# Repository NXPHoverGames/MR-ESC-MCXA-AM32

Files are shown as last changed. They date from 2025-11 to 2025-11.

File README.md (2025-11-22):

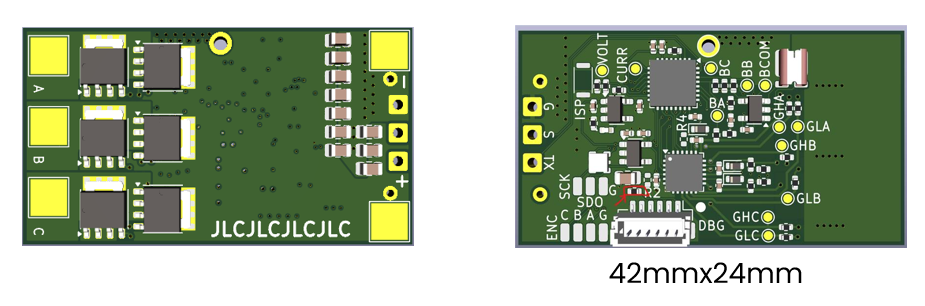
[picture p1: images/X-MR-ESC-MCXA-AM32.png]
Rendering of x-MR-ESC-MCXA-AM32 board


MR-ESC-MCXA-AM32 is a proof of concept Drone motor ESC (Electronic Speed Controller) motor controller, 
using NXP MCXA153 MCU and running the opensource AM32 software.

NOTE: This design is not supported by NXP motor control framework tools 
(it could of course be made to run with modifications)

Design files are in KiCAD.

Target MCU in AM32 directories is "a153"
Upstream repository for AM32 is here:
https://github.com/AlkaMotors/AM32-MultiRotor-ESC-firmware/tree/master

Interim AM32 enablement for MR-ESC-MCXA-AM32 is here:
(It will be upstreamed)
repo:NXPHoverGames/AM32-MultiRotor-ESC-firmware-MCXA
https://github.com/NXPHoverGames/AM32-MultiRotor-ESC-firmware-MCXA

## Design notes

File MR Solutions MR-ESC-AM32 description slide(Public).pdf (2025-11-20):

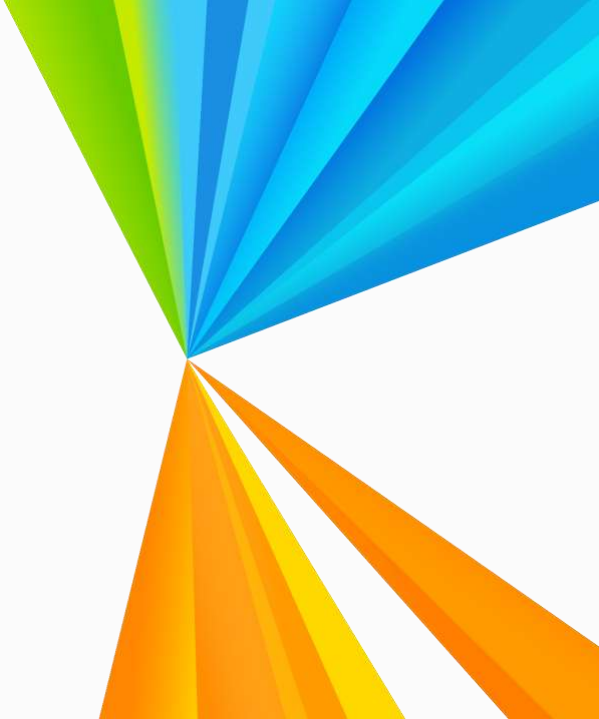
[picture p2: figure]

| Public | NXP and the NXP logo are trademarks of NXP B.V. All other product
or service names are the property of their respective owners. © 2024 NXP B.V.

## Iain Galloway Mobile Robotics, System Innovations CTO R&D

## March 2025

## Proof of concept MCX ESC using AM32

opensource software.

# NXP Mobile Robotics

# MR-ESC-AM32 Proof of Concept only

## MCXA MCU: NXP MCXA153

- Simple trapezoidal ESC motor controller with RC-PWM input.
- Form factor for Drones and small devices.
- Copy of AM32 reference hardware to establish NXP Baseline
- Low cost ~$10 target
Justification:
- AM32 is popular opensource ESC software.
- Engage with community
- Include NXP Solution in NXP HoverGames drone EVK
- Future MR-HGK-RT
- Hooks in place for QDEC where odometry is needed such as ground applications. MR-B3RB-M, MELM.
Specs –approx.:
- 5.5V up to 24V, 6 Cell/6S LiPo battery input voltage
- Onboard PSMN1R4-40 FETs rated 240A
– note this is not the board rating
- 50A peak drain seems likely
- In-situ current rating TBD, required validation testing, dependent on heatsinking added.
Future potential options:
- Enable QDEC input
- Enable NXP software
- Revise design to use MCXA16x
(Analog integration lower bom cost)
- Enable NXP FOC as alternative software.
- Add CAN interface
- Consider advanced version using MCXN with FOC, NPU enable motor analysis, T1 Ethernet interface

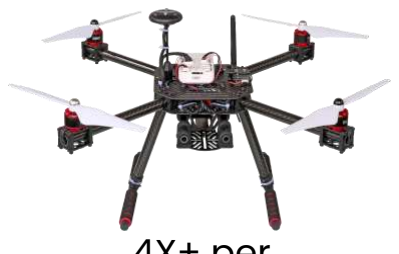
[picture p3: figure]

## 4X+ per Drone

MCU | Gate Driver
RC-PWM | FETs

Simple
Trapezoidal

Approx BOM
$1.68 MCU
$0.75 Gate Drv
$0.13 opAmp
$6.40 FETs 8x$0.80*
$0.18 regulator
$0.18 regulator
$1-2 PCB, passives, connectors -=-=-
$11.42
*FET selection is cost driver.

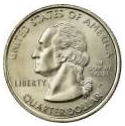
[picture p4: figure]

42mmx24mm

3 | NXP | Internal

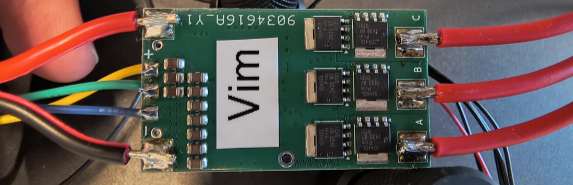
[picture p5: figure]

Wire the + and - input to the power supply (6V to 24V max). The board does not have polarity protection so make sure you have wired the + and - correctly.

Wire signal pin (indicated with "S" on board) to the function generator which should generate a PWM signal with Low voltage at 0V and High voltage at 3.3V. PWM signal must have a period of 2.2ms. Motor starts spinning from 50% duty cycle up to 99%.

Wire ground pin (indicated with "G" on board) to the ground of the function generator.

TX pin may connect to a serial data converter (e.g. FTDI cable). This is not mandatory for the board to work.

Wire motor phase outputs (A, B and C) to each motor phase.

Test pads:

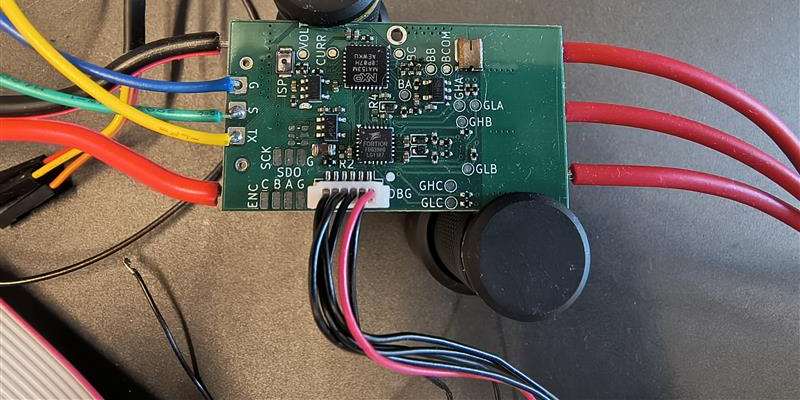
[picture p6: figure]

- Test pad GHA, GHB and GHC are the high MOSFET gate signals of each corresponding phase.
- Test pad GLA, GLB and GLC are the low MOSFET gate signals of each corresponding phase.
- Test pad BA, BB and BC are the BEMF signals of each corresponding phase.
- Test pad BCOM is the BEMF common signal.
- Test pad VOLT is tied to the voltage sense input of the MCU.
- Test pad CURR is tied to the current sense input of the MCU.

# Wiring (DRAFT – for debugging purposes)

For debug purposes you can optionally use the pads "ENC A" and "ENC C" as GPIO. The "G" pad near the ENC pads is a ground.

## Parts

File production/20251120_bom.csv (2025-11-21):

Designator | Footprint | Quantity | Value | LCSC Part #
C1, C10, C15, C2, C3, C4, C5, C6, C7, C8, C9 | 0805 | 11 | 10uF 35V
C12, C19, C23 | 0402 | 3 | 1uF 16V
C13, C14, C16, C24, C25 | 0402 | 5 | 100nF 16V
C17, C20, C21 | 0603 | 3 | 1uF 50V
C18, C22 | 0402 | 2 | 100nF 50V
D1, D2, D3 | D_SOD-523 | 3 | 1N4148WT
D4 | 0402 | 1 | LED GREEN
J13 | JST_SH_BM06B-SRSS-TB_1x06-1MP_P1.00mm_Vertical | 1 | DEBUG
Q1, Q2, Q3, Q4, Q5, Q6 | LFPAK56 | 6 | PSMN1R4-40YLDX
R1, R10, R11, R12, R13, R24, R3, R8, R9 | 0402 | 9 | 10k
R14, R15, R16, R22 | 0402 | 4 | 1k
R17, R18, R19, R5, R6, R7 | 0402 | 6 | 20
R20 | 0402 | 1 | 100k
R21 | WSK1216 | 1 | 1m 3W
R23 | 0402 | 1 | 2.2k
R25 | 0402 | 1 | 100R
SW1 | TS2306A | 1 | ISPMODE
U1 | SOT-23-5 | 1 | TPS7B92033DBVR
U2 | VQFN-24-1EP_4x4mm_P0.5mm_EP2.45x2.45mm | 1 | DRV8300N or FD6288 or equivalent
U3 | HVQFN-32-1EP_5x5mm_P0.5mm_EP3.1x3.1mm | 1 | MCXA1xxVFM
U4 | SOT-23-5 | 1 | TPS7B92050DBVR
U5 | BB-2020BGR-TRB | 1 | BB-2020BGR-TRB
U6 | SOT-23-5 | 1 | INA180B1

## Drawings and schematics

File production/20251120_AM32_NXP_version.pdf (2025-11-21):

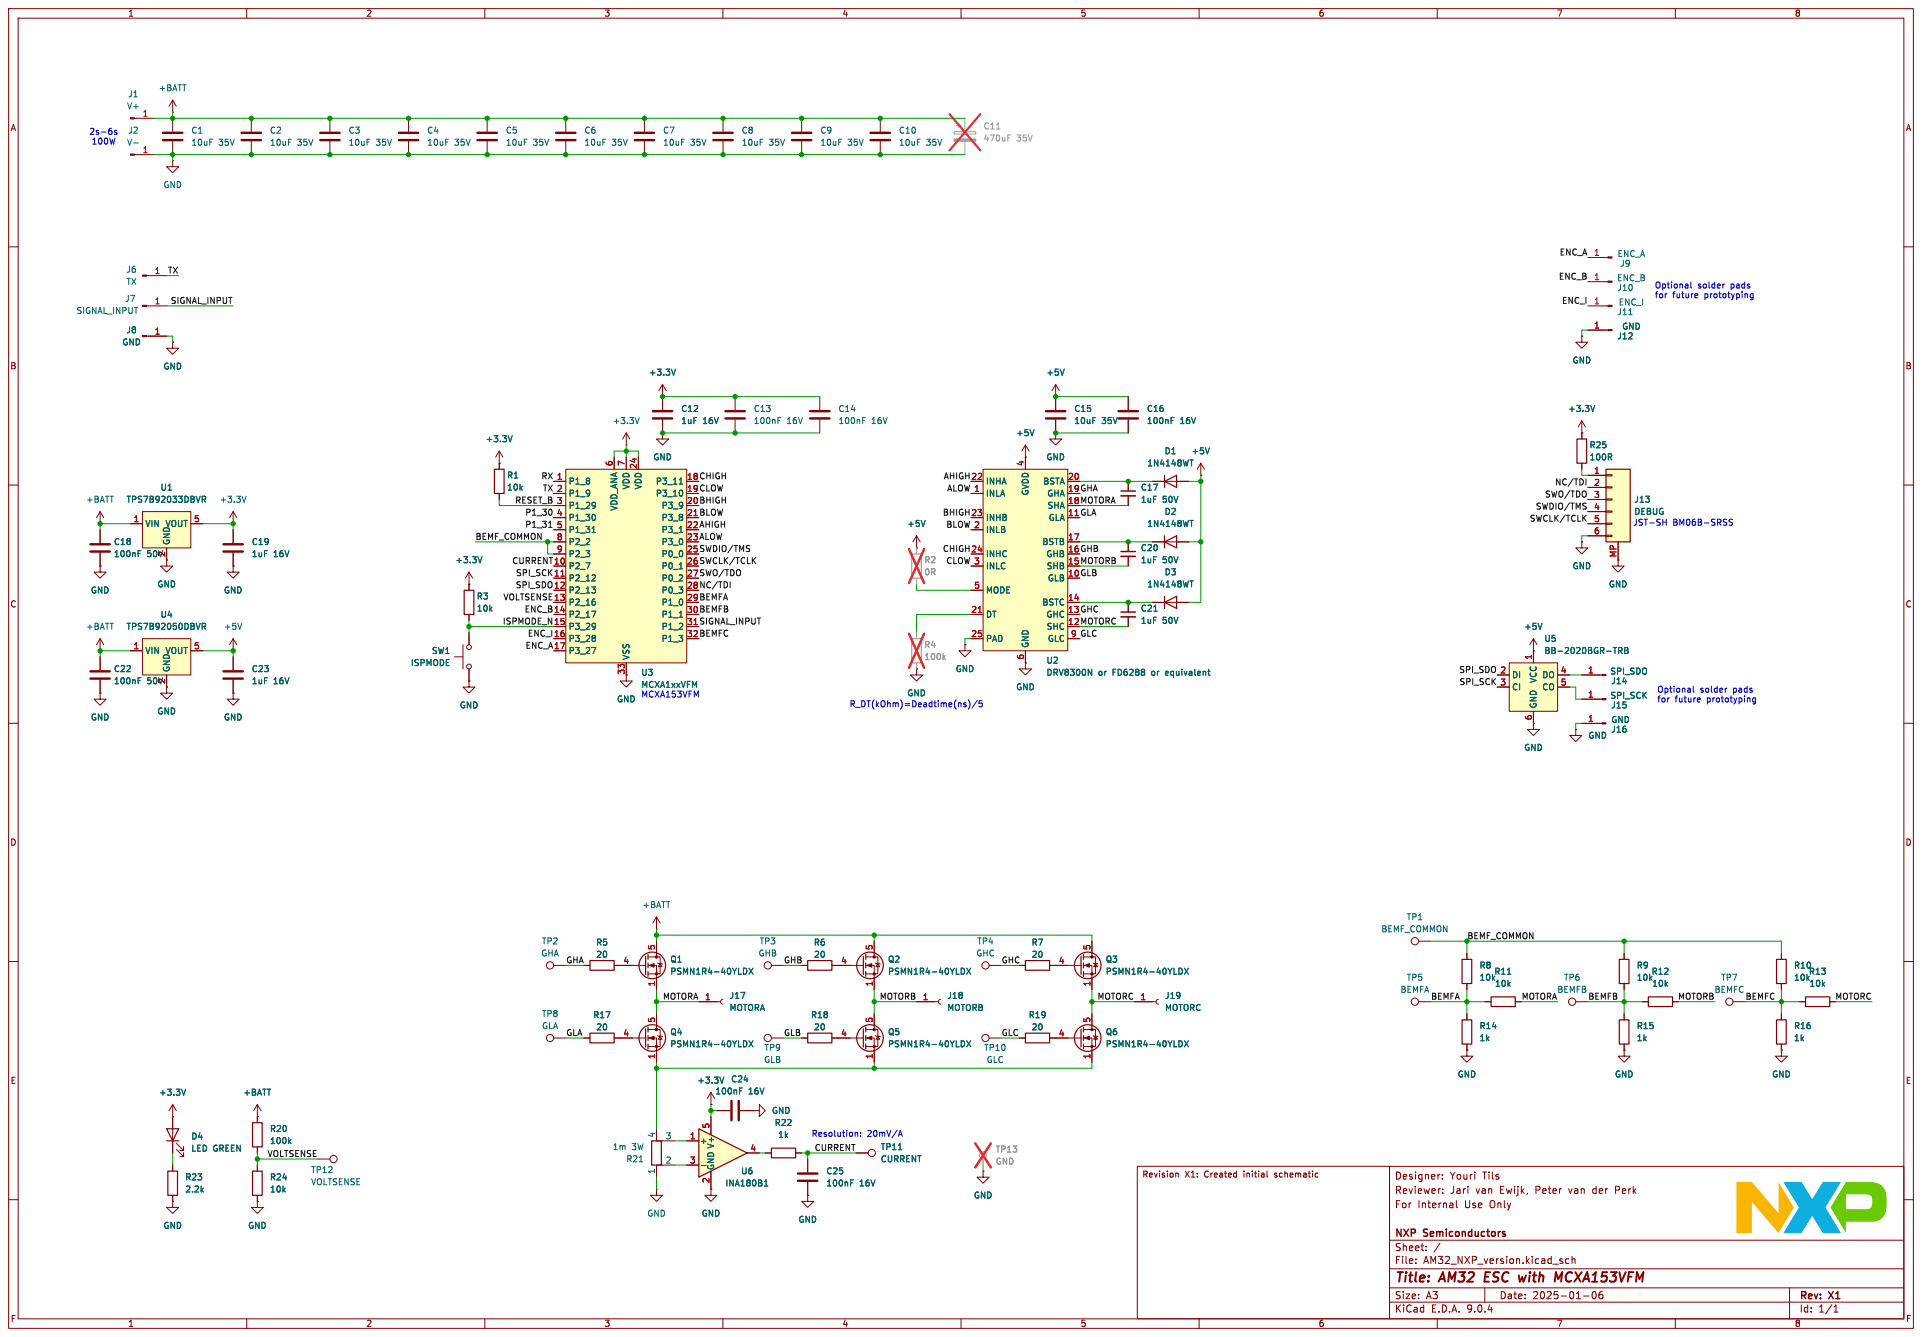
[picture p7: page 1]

6 BSTA 20 GHA 19 SHA 18 GLA 11 BSTB 17 GHB 16 SHB 15 GLB 10 BSTC 14 GHC 13 SHC 12 GLC 9 U2 DRV8300N or FD6288 or equivalent D3

6 BSTA 20 GHA 19 SHA 18 GLA 11 BSTB 17 GHB 16 SHB 15 GLB 10 BSTC 14 GHC 13 SHC 12 GLC 9 D3

Id: 1/1 Title: AM32 ESC with MCXA153VFM

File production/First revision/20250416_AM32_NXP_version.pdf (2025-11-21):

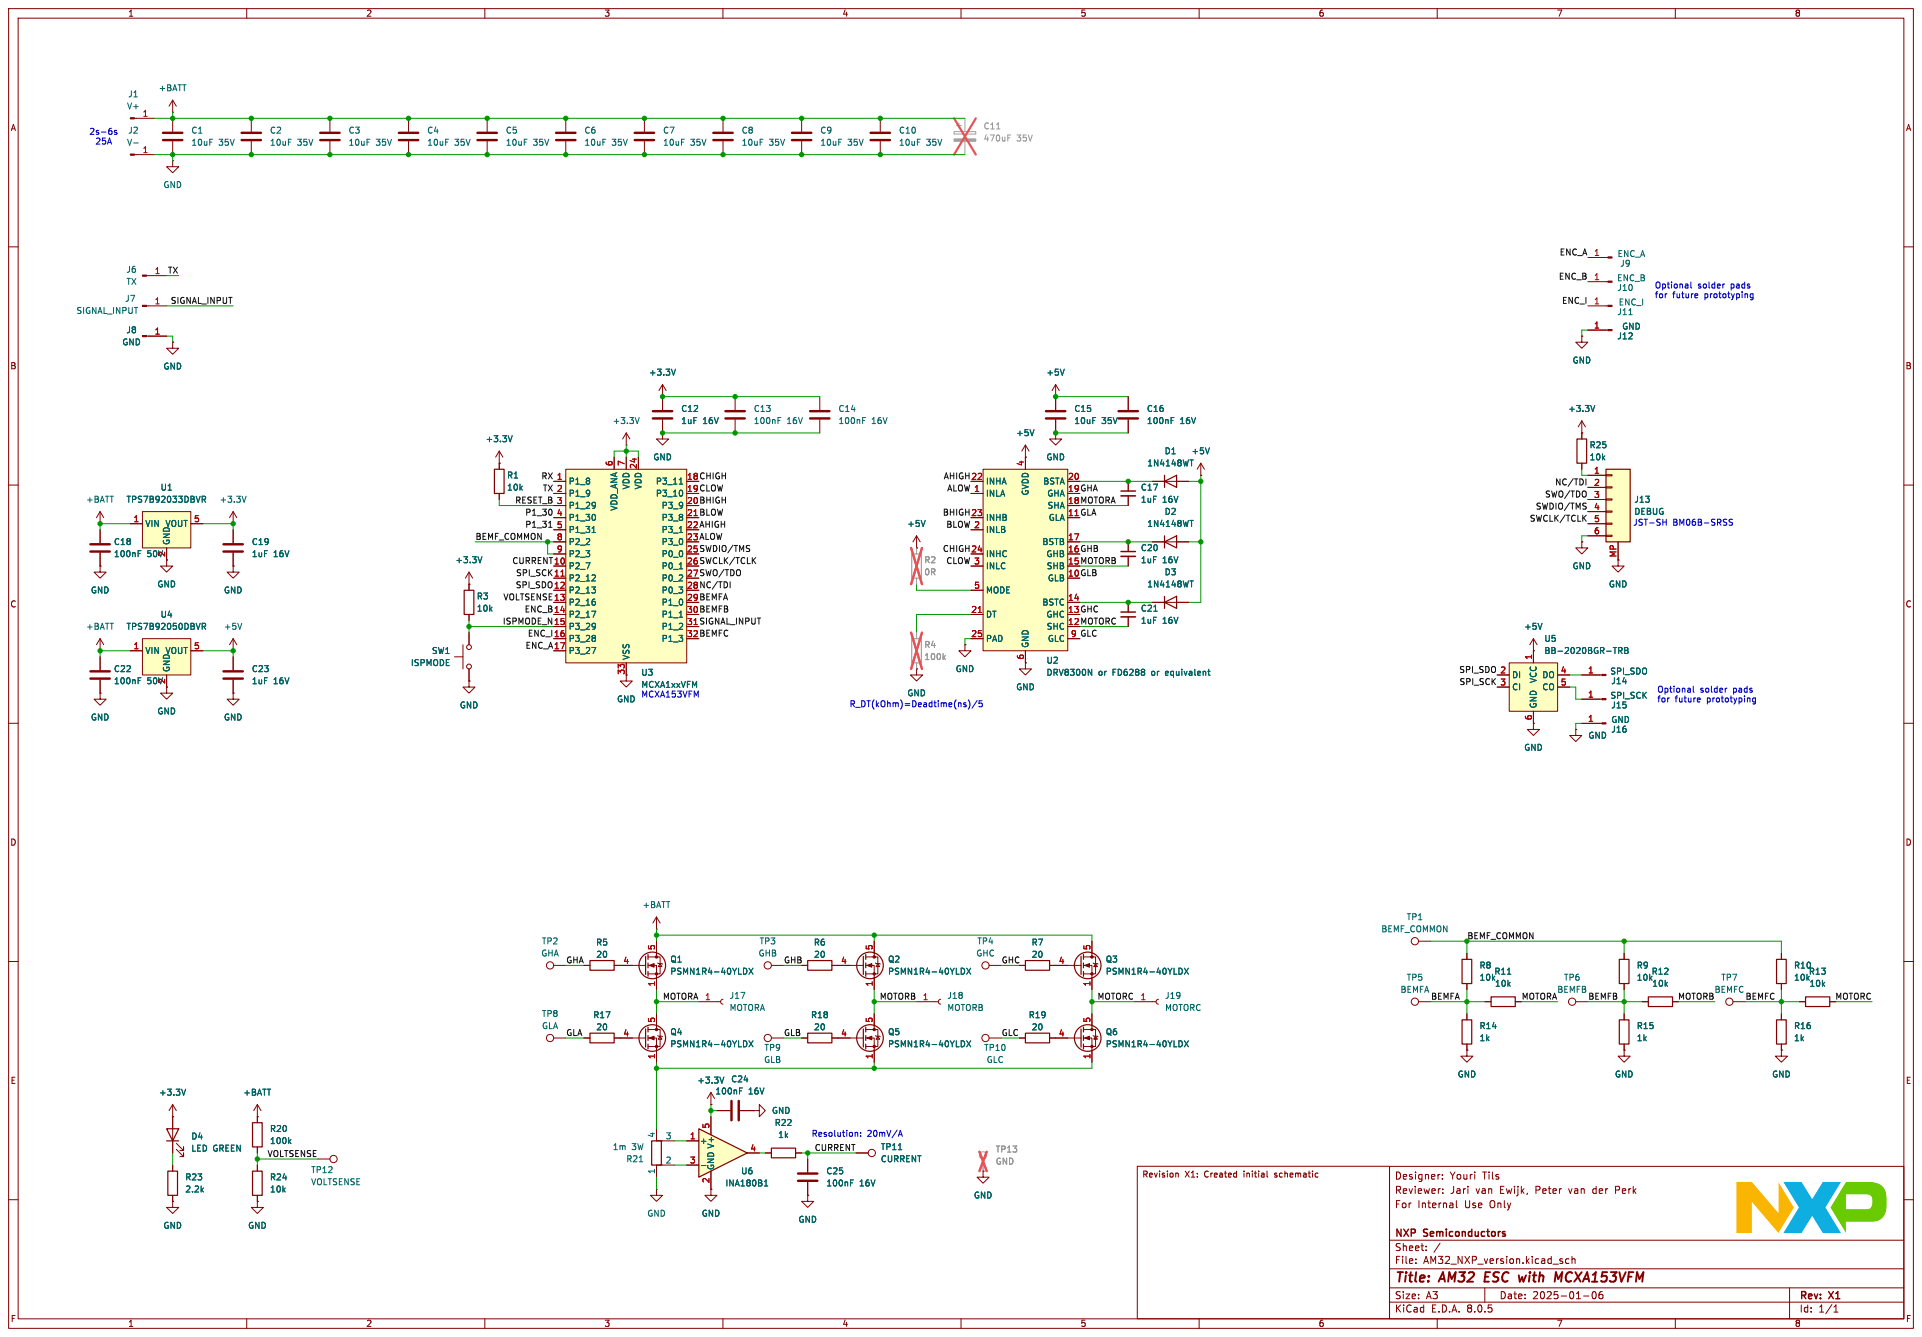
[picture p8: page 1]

NC/TDI GHB MOTORB GLB MOTORC GLC GHC GLA MOTORA GHA

6 GLC 9 U2 DRV8300N or FD6288 or equivalent C21
1uF 16V U2 DRV8300N or FD6288 or equivalent

1 DI 2 CI 3 DO 4 CO 5 GND

Id: 1/1 Title: AM32 ESC with MCXA153VFM

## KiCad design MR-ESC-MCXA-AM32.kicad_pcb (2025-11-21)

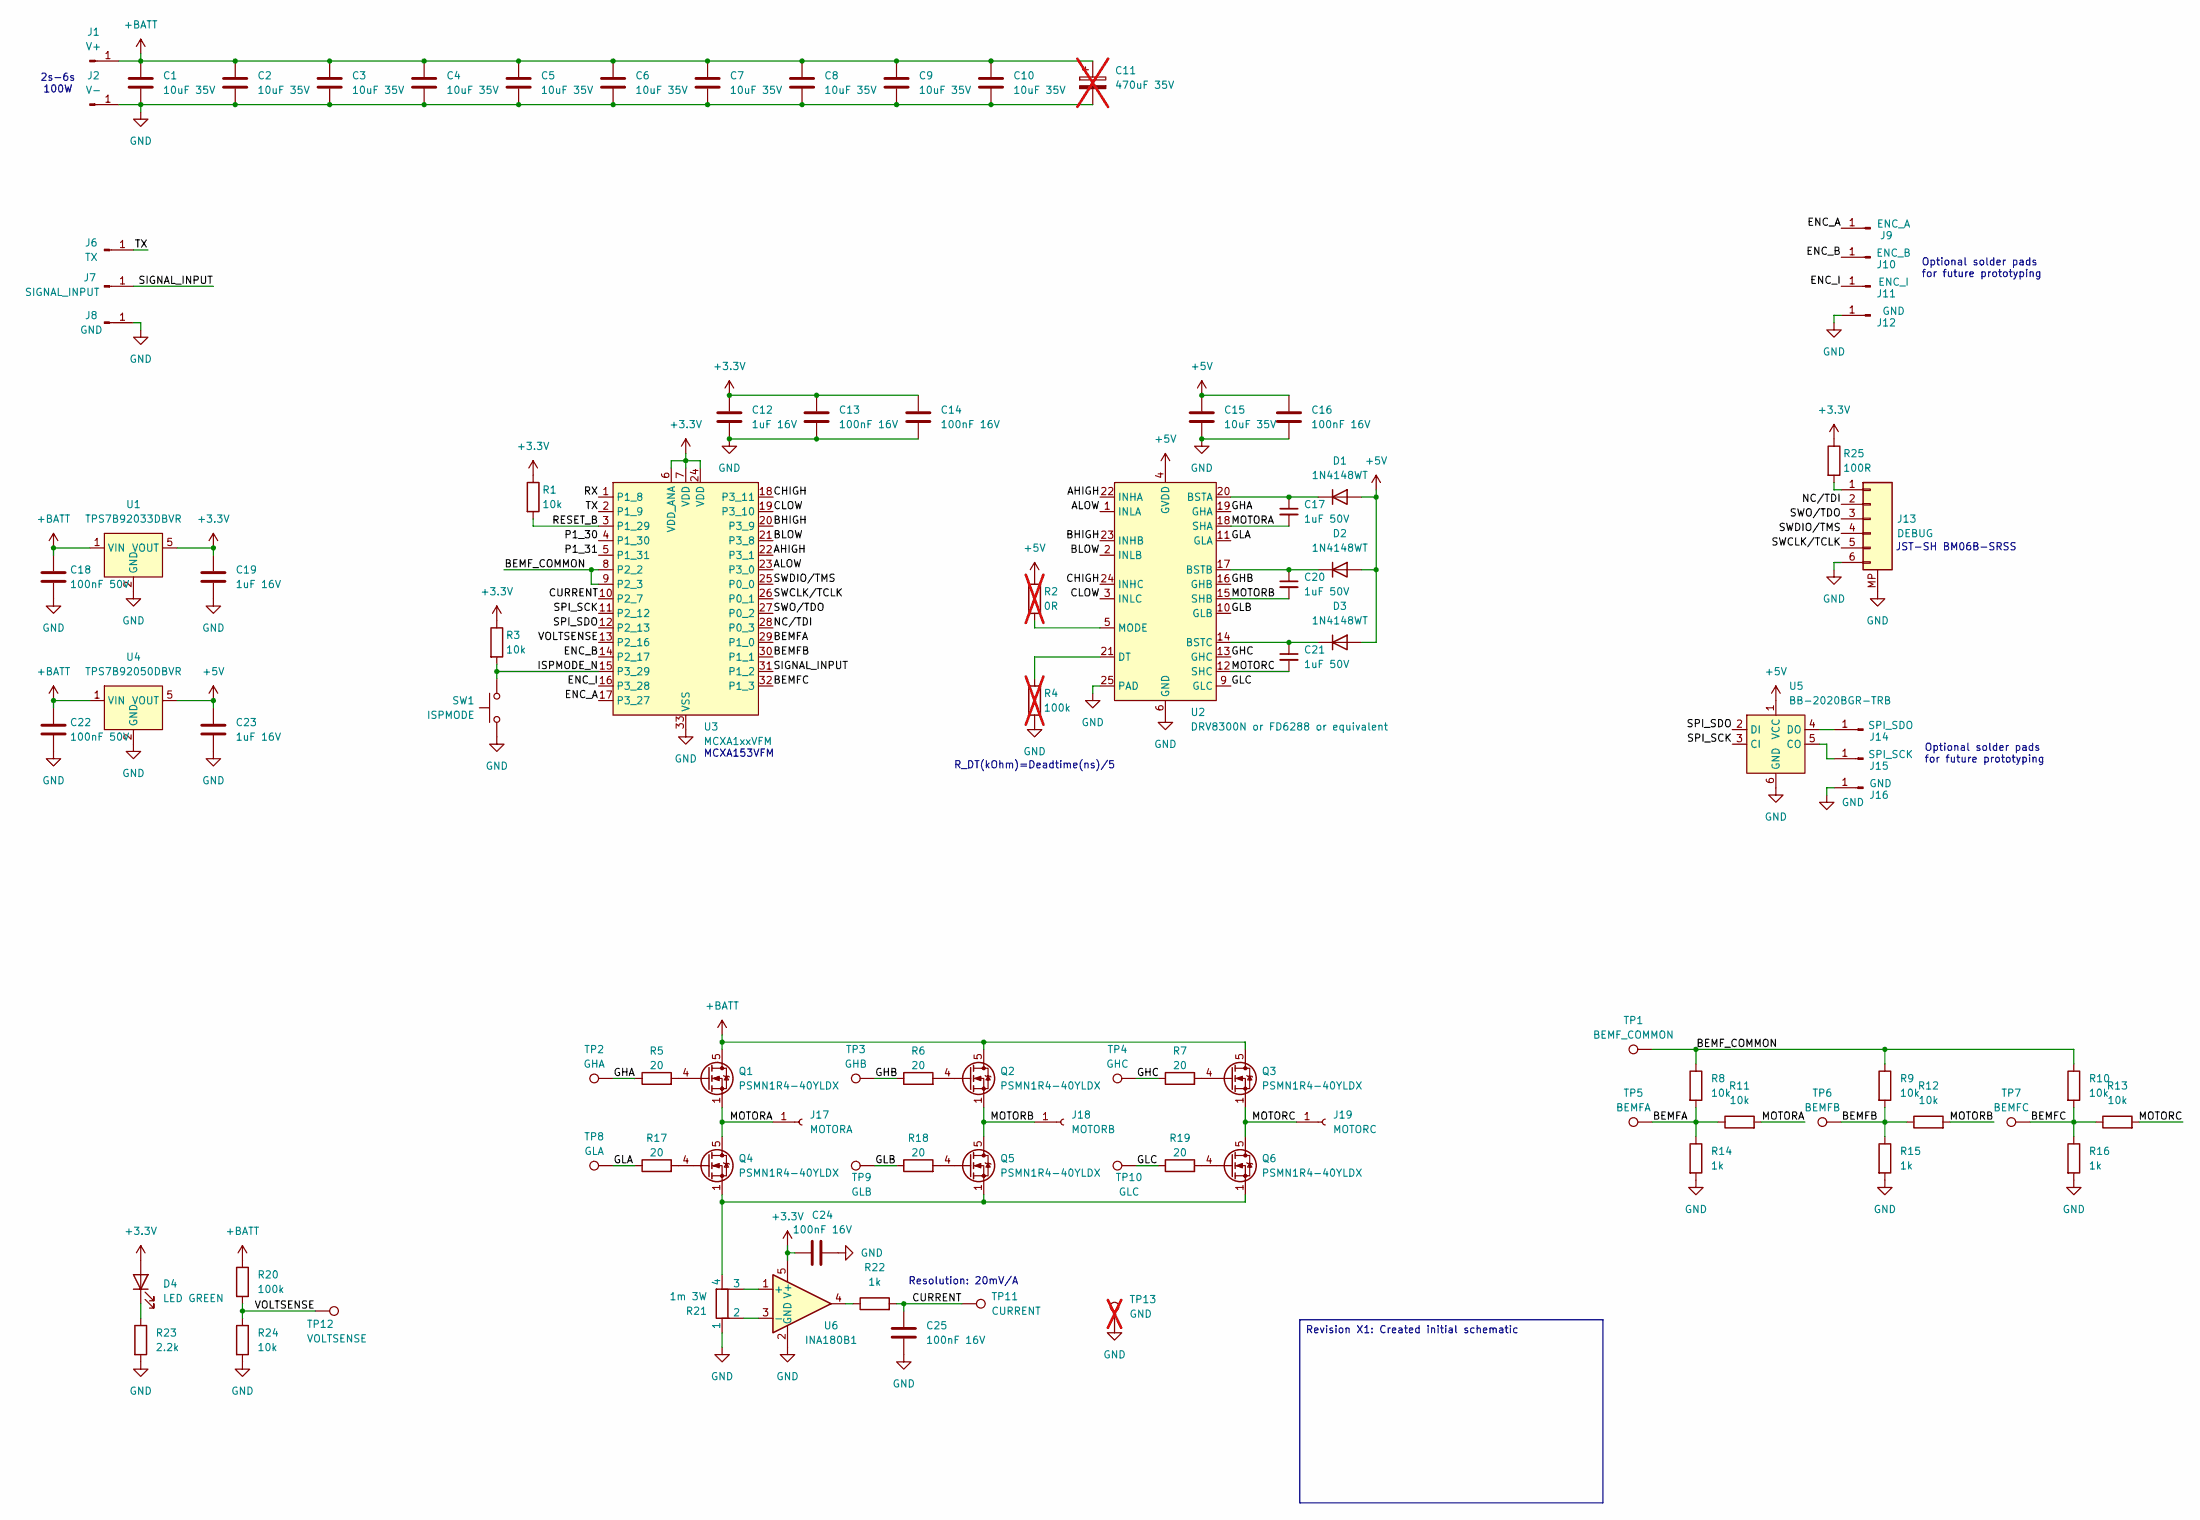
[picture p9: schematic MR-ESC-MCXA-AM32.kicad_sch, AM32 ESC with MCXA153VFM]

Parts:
C1, C2, C3, C4, C5, C6, C7, C8, C9, C10, C15: 10uF 35V; C_0805_2012Metric
C11: 470uF 35V; C_Axial_L3.8mm_D2.6mm_P12.50mm_Horizontal; not fitted
C12, C19, C23: 1uF 16V; C_0402_1005Metric
C13, C14, C16, C24, C25: 100nF 16V; C_0402_1005Metric
C17, C20, C21: 1uF 50V; C_0603_1608Metric
C18, C22: 100nF 50V; C_0402_1005Metric
D1, D2, D3: 1N4148WT; D_SOD-523
D4: LED GREEN; LED_0402_1005Metric
J1: V+; TestPoint_Pad_4.0x4.0mm
J2: V-; TestPoint_Pad_4.0x4.0mm
J6: TX; SolderWire-0.5sqmm_1x01_D0.9mm_OD2.1mm
J7: SIGNAL_INPUT; SolderWire-0.5sqmm_1x01_D0.9mm_OD2.1mm
J8: GND; SolderWire-0.5sqmm_1x01_D0.9mm_OD2.1mm
J9: ENC_A; SolderWirePad_1x01_SMD_1x2mm
J10: ENC_B; SolderWirePad_1x01_SMD_1x2mm
J11: ENC_I; SolderWirePad_1x01_SMD_1x2mm
J12, J16: GND; SolderWirePad_1x01_SMD_1x2mm
J13: DEBUG; JST_SH_BM06B-SRSS-TB_1x06-1MP_P1.00mm_Vertical
J14: SPI_SDO; SolderWirePad_1x01_SMD_1x2mm
J15: SPI_SCK; SolderWirePad_1x01_SMD_1x2mm
J17: MOTORA; TestPoint_Pad_4.0x4.0mm
J18: MOTORB; TestPoint_Pad_4.0x4.0mm
J19: MOTORC; TestPoint_Pad_4.0x4.0mm
Q1, Q2, Q3, Q4, Q5, Q6: PSMN1R4-40YLDX; LFPAK56
R1, R3, R8, R9, R10, R11, R12, R13, R24: 10k; R_0402_1005Metric
R2: 0R; R_0402_1005Metric; not fitted
R4: 100k; R_0402_1005Metric; not fitted
R5, R6, R7, R17, R18, R19: 20; R_0402_1005Metric
R14, R15, R16, R22: 1k; R_0402_1005Metric
R20: 100k; R_0402_1005Metric
R21: 1m 3W; WSK1216
R23: 2.2k; R_0402_1005Metric
R25: 100R; R_0402_1005Metric
SW1: ISPMODE; TS2306A
TP1: BEMF_COMMON; TestPoint_Pad_D1.0mm
TP2: GHA; TestPoint_Pad_D1.0mm
TP3: GHB; TestPoint_Pad_D1.0mm
TP4: GHC; TestPoint_Pad_D1.0mm
TP5: BEMFA; TestPoint_Pad_D1.0mm
TP6: BEMFB; TestPoint_Pad_D1.0mm
TP7: BEMFC; TestPoint_Pad_D1.0mm
TP8: GLA; TestPoint_Pad_D1.0mm
TP9: GLB; TestPoint_Pad_D1.0mm
TP10: GLC; TestPoint_Pad_D1.0mm
TP11: CURRENT; TestPoint_Pad_D1.0mm
TP12: VOLTSENSE; TestPoint_Pad_D1.0mm
TP13: GND; TestPoint_THTPad_D2.0mm_Drill1.0mm; not fitted
U1: TPS7B92033DBVR; SOT-23-5
U2: DRV8300N or FD6288 or equivalent; VQFN-24-1EP_4x4mm_P0.5mm_EP2.45x2.45mm
U3: MCXA1xxVFM; HVQFN-32-1EP_5x5mm_P0.5mm_EP3.1x3.1mm
U4: TPS7B92050DBVR; SOT-23-5
U5: BB-2020BGR-TRB
U6: INA180B1; SOT-23-5

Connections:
+3.3V: C12.1, C13.1, C14.1, C19.1, C24.1, D4.2 (A), R1.1, R3.1, R25.1, U1.5 (VOUT), U3.6 (VDD_ANA), U3.7 (VDD), U3.24 (VDD), U6.5 (V+)
+5V: C15.1, C16.1, C23.1, D1.2 (A), D2.2 (A), D3.2 (A), R2.1, U2.4 (GVDD), U4.5 (VOUT), U5.1 (VCC)
+BATT: C1.1, C2.1, C3.1, C4.1, C5.1, C6.1, C7.1, C8.1, C9.1, C10.1, C11.1, C18.1, C22.1, J1.1, Q1.5 (D), Q2.5 (D), Q3.5 (D), R20.1, U1.1 (VIN), U4.1 (VIN)
/AHIGH: U2.22 (INHA), U3.22 (P3_1)
/ALOW: U2.1 (INLA), U3.23 (P3_0)
/BEMFA: R8.2, R11.1, R14.1, TP5.1, U3.29 (P1_0)
/BEMFB: R9.2, R12.1, R15.1, TP6.1, U3.30 (P1_1)
/BEMFC: R10.2, R13.1, R16.1, TP7.1, U3.32 (P1_3)
/BEMF_COMMON: R8.1, R9.1, R10.1, TP1.1, U3.8 (P2_2), U3.9 (P2_3)
/BHIGH: U2.23 (INHB), U3.20 (P3_9)
/BLOW: U2.2 (INLB), U3.21 (P3_8)
/CHIGH: U2.24 (INHC), U3.18 (P3_11)
/CLOW: U2.3 (INLC), U3.19 (P3_10)
/CURRENT: C25.1, R22.2, TP11.1, U3.10 (P2_7)
/ENC_A: J9.1, U3.17 (P3_27)
/ENC_B: J10.1, U3.14 (P2_17)
/ENC_I: J11.1, U3.16 (P3_28)
/GHA: R5.1, TP2.1, U2.19 (GHA)
/GHB: R6.1, TP3.1, U2.16 (GHB)
/GHC: R7.1, TP4.1, U2.13 (GHC)
/GLA: R17.1, TP8.1, U2.11 (GLA)
/GLB: R18.1, TP9.1, U2.10 (GLB)
/GLC: R19.1, TP10.1, U2.9 (GLC)
/ISPMODE_N: R3.2, SW1.1, U3.15 (P3_29)
/MOTORA: C17.2, J17.1, Q1.1 (S), Q1.2 (S), Q1.3 (S), Q4.5 (D), R11.2, U2.18 (SHA)
/MOTORB: C20.2, J18.1, Q2.1 (S), Q2.2 (S), Q2.3 (S), Q5.5 (D), R12.2, U2.15 (SHB)
/MOTORC: C21.2, J19.1, Q3.1 (S), Q3.2 (S), Q3.3 (S), Q6.5 (D), R13.2, U2.12 (SHC)
/NC/TDI: J13.2, U3.28 (P0_3)
/P1_30: U3.4 (P1_30)
/P1_31: U3.5 (P1_31)
/RESET_B: R1.2, U3.3 (P1_29)
/RX: U3.1 (P1_8)
/SIGNAL_INPUT: J7.1, U3.31 (P1_2)
/SPI_SCK: U3.11 (P2_12), U5.3 (CI)
/SPI_SDO: U3.12 (P2_13), U5.2 (DI)
/SWCLK/TCLK: J13.5, U3.26 (P0_1)
/SWDIO/TMS: J13.4, U3.25 (P0_0)
/SWO/TDO: J13.3, U3.27 (P0_2)
/TX: J6.1, U3.2 (P1_9)
/VOLTSENSE: R20.2, R24.1, TP12.1, U3.13 (P2_16)
GND: C1.2, C2.2, C3.2, C4.2, C5.2, C6.2, C7.2, C8.2, C9.2, C10.2, C11.2, C12.2, C13.2, C14.2, C15.2, C16.2, C18.2, C19.2, C22.2, C23.2, C24.2, C25.2, J2.1, J8.1, J12.1, J13.6, J13.MP, J16.1, R4.2, R14.2, R15.2, R16.2, R21.1, R23.2, R24.2, SW1.2, TP13.1, U1.2 (GND), U2.6 (GND), U2.25 (PAD), U3.33 (VSS), U4.2 (GND), U5.6 (GND), U6.2 (GND)
unnamed: C17.1, D1.1 (K), U2.20 (BSTA)
unnamed: C20.1, D2.1 (K), U2.17 (BSTB)
unnamed: C21.1, D3.1 (K), U2.14 (BSTC)
unnamed: D4.1 (K), R23.1
unnamed: J13.1, R25.2
unnamed: J14.1, U5.4 (DO)
unnamed: J15.1, U5.5 (CO)
unnamed: Q1.4 (G), R5.2
unnamed: Q2.4 (G), R6.2
unnamed: Q3.4 (G), R7.2
unnamed: Q4.4 (G), R17.2
unnamed: Q4.1 (S), Q4.2 (S), Q4.3 (S), Q5.1 (S), Q5.2 (S), Q5.3 (S), Q6.1 (S), Q6.2 (S), Q6.3 (S), R21.4
unnamed: Q5.4 (G), R18.2
unnamed: Q6.4 (G), R19.2
unnamed: R22.1, U6.4
unnamed: R4.1, U2.21 (DT)
unnamed: R2.2, U2.5 (MODE)
unnamed: R21.3, U6.1 (+)
unnamed: R21.2, U6.3 (-)

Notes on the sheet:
Optional solder pads for future prototyping
JST-SH BM06B-SRSS
R_DT(kOhm)=Deadtime(ns)/5
Resolution: 20mV/A
2s-6s 100W
MCXA153VFM
Revision X1: Created initial schematic

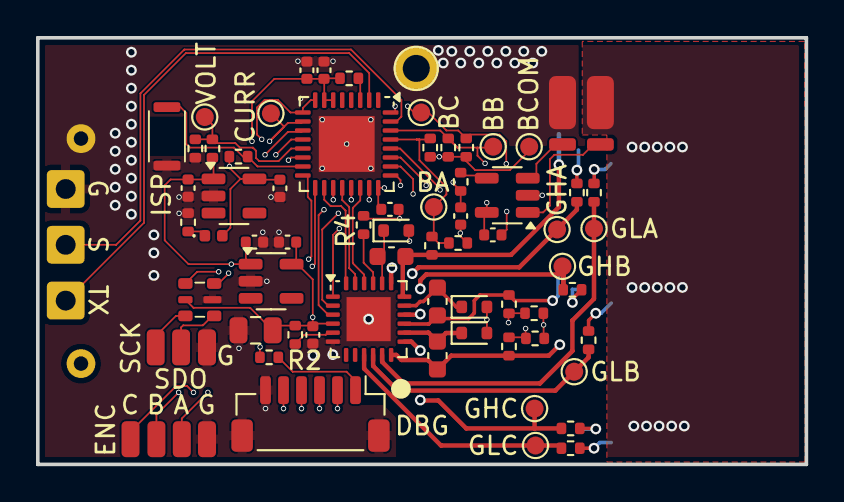
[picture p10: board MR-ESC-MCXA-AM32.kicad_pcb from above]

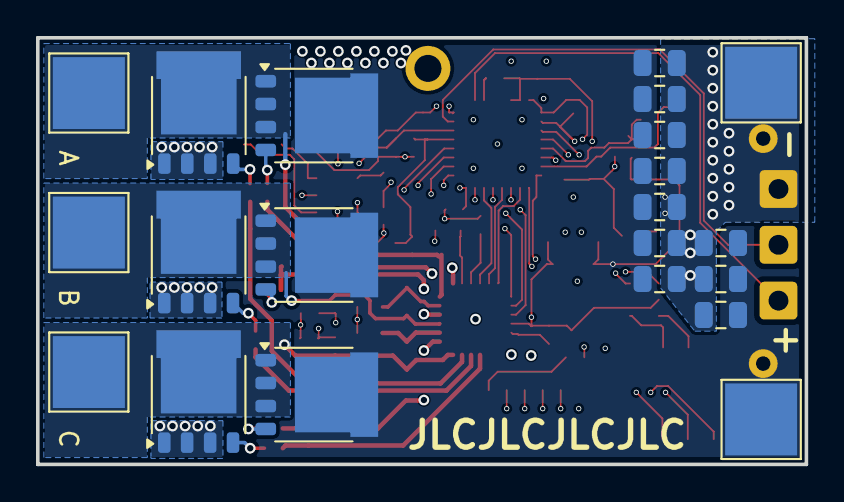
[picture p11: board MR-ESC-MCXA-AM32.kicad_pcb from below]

Board: 4 copper layers, 42.7 x 23.7 mm, 96 parts (21 on the bottom side), 57 nets.

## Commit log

2025-11-20 Create MR Solutions MR-ESC-AM32 description slide(Public).pdf
2025-11-21 First commit of motor control pcb with MCXA133 for AM32 motor control. Schematic is finished. Only connectors could be changed in the future. PCB layout has been started on.
    [AM32_NXP_version.kicad_pcb, AM32_NXP_version.kicad_sch]
2025-11-21 Added connectors for all inputs and outputs. Added correct part numbers in components for the BOM generation. Added test points for gates, BEMF, current and voltage. Schematic is as good as finished.
    [AM32_NXP_version.kicad_pcb, AM32_NXP_version.kicad_sch]
2025-11-21 Updated schematic with feedback. Updated Layout.
    [AM32_NXP_version.kicad_pcb, AM32_NXP_version.kicad_sch]
2025-11-21 Added BB-2020BGR-TRB component symbol, footprint and 3d-model. Replaced APA102 with BB-2020BGR-TRB
2025-11-21 Added custom design rule for silkscreen clearance.
2025-11-21 Added NXP template and changed schematic size to A3.
2025-11-21 Added files that tell Kicad where the footprint and symbol are located.
2025-11-21 Added fabrication-toolkit-options file used by Kicad for exporting fabrication files for JLCPCB.
2025-11-21 Updated schematic further after feedback session. Finalized the schematic. Updated the layout and finalized it for reviewing.
    [AM32_NXP_version.kicad_pcb, AM32_NXP_version.kicad_sch]
2025-11-21 Added 3D files for JST header, MCXA153 and DRV8300.
    [AM32_NXP_version.kicad_pcb]
2025-11-21 Updated layout after review session. Made all non-power vias smaller. Made high current return path wider. Added JLCPCB switch and made footprint for this. Removed most of the silkscreen and made sil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
    [AM32_NXP_version.kicad_pcb, AM32_NXP_version.kicad_sch]
2025-11-21 Cleared up unnecessary silkscreen and added silkscreen for test points.
    [AM32_NXP_version.kicad_pcb]
2025-11-21 Created PDF of schematic. Created production files for JLCPCB ordering.
    [AM32_NXP_version.kicad_pcb, AM32_NXP_version.kicad_sch, bom.csv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]
2025-11-21 Added revision list in schematic. Specified use of MCXA153VFM and added alternative components to DRV8300 name. Made thermal relief of 3W current sense resistor solid. Removed the ground planes near 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
    [AM32_NXP_version.kicad_pcb, AM32_NXP_version.kicad_sch, bom.csv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]
2025-11-21 Updated production Gerber file
2025-11-21 Patched board
    - Updated boost caps to 50V
    - Updated 10k resistor at debug header to 100R
    - Replaced MCXA153 with MCXA133
    - Updated layout to implement changes
    [AM32_NXP_version.kicad_pcb, AM32_NXP_version.kicad_sch]
2025-11-21 Created JLCPCB production files of latest version and added history of production
    - Created production files of latest version including schematic pdf.
    - Moved old production files to first revision folder with date.
    [20250416_bom.csv, 20250416_designators.csv, 20250416_positions.csv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]
2025-11-21 Renamed files
    [AM32_NXP_version.kicad_pcb, AM32_NXP_version.kicad_sch, MR-ESC-MCXA-AM32.kicad_pcb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]
